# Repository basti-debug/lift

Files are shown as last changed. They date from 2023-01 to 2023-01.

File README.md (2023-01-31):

# Liftsteuerung

*** 

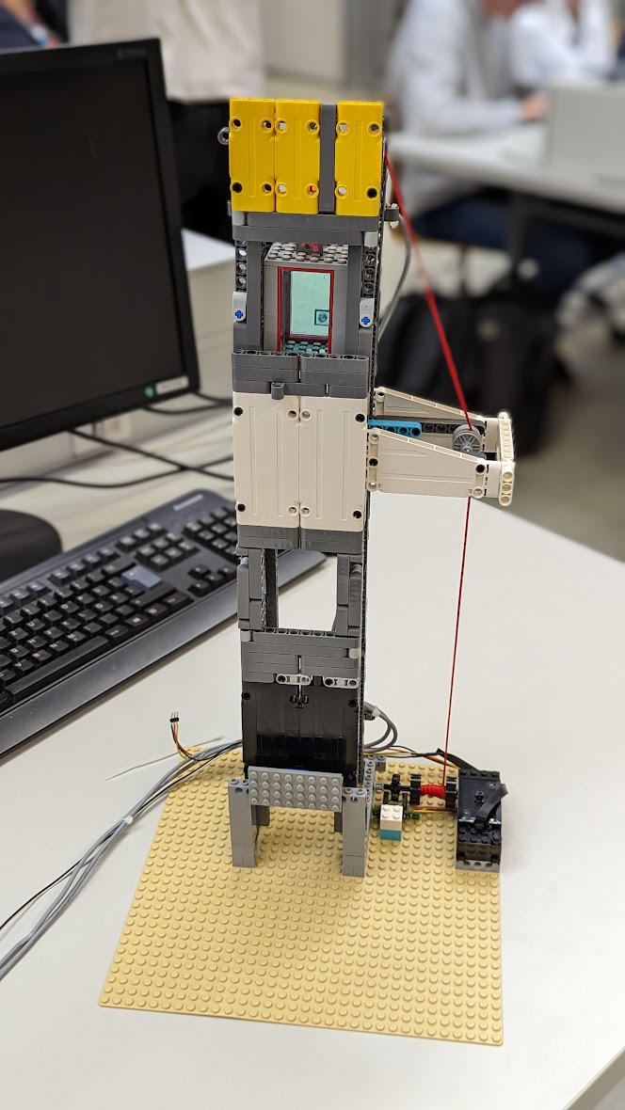
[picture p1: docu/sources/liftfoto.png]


Projektmitglieder: 
* Sebastian Mayrhofer / *zuständig für Hardware und Dokumentation*
* Joel Rupp / *zuständig für Software*

 **HTL Rankweil**  4chel                                                                 Schuljahr 2022-23 

***

[TOC]

***

## Aufgabenstellung 
*verfasst von Sebastian Mayrhofer*

Im Projekt "Liftsteuerung" wird dass Konzept einer Liftsteuerung in Miniatur umgesetzt. Der Lift soll mit Hilfe von Lego Componenten und einer MegaCard gesteuert werden. Mit Hilfe einer Lichtschranke soll die Position der Kabine herausgefunden werden. Ebenfalls wird ein Hall Sensor als Endstop genutzt. 

## Umsetzung 
Uns wurde ein motorisierter Liftschacht aus Lego zur Verfügung gestellt. Wir haben den Liftschacht verstärkt und der Kabine Rollen montiert, die die Fahrt stabilisieren sollen. 

### Benutztes Material

* Lego-Steine  (Lift Schacht und Kabine) 
* MEGACard  (Steuerung des Motors, auswertung der Sensoren)
* Hall Sensor (End-Stop)
* Lichtschranke (Stockwerkbestimmung)

### Stockwerk-bestimmung (Lichtschranke)

Da nach einem Reset die Position des Liftes unbekannt ist, muss irgendwie ein bestimmer Zustand hergestellt werden. Dies ist bei uns so realisiert, indem der Aufzug nach unten fährt, bis der untere Endstop auslöst. Dann wir die Höhe genullt

Um die Stockwerke genau zu bestimmen, benutzen wir, wie vorgegeben, eine Lichtschranke. Diese Lichtschranke wurde unterbrochen durch ein Lego Technik Teil das wir direkt auf Antriebsachse (Winden Achse) gesteckt haben.

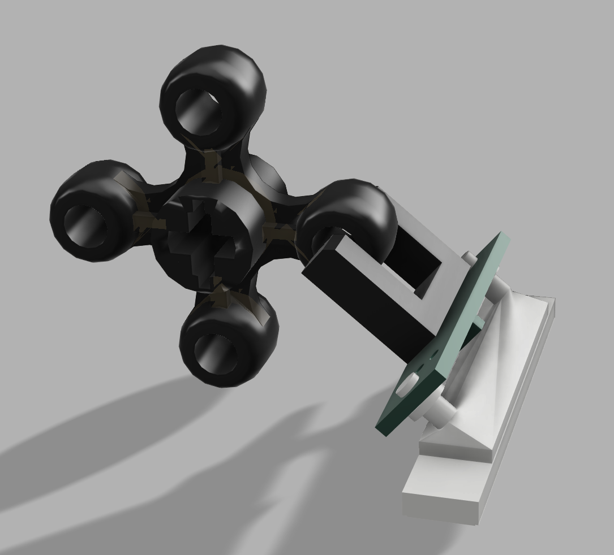
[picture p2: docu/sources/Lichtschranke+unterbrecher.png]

*Lichtschranke Halterung mit Unterbrecher*

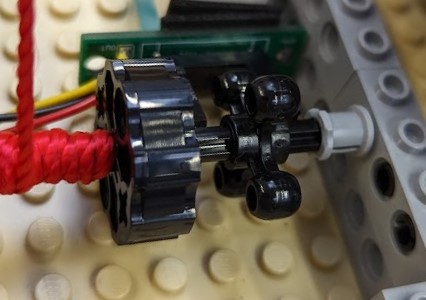
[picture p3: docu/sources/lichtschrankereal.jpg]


*realer Aufbau*

**Wie Messen wir mit Hilfe der Lichtschranke ?** 

Mit Hilfe eines externen Interrupts der auf die fallende Flanke des Sensors (also das Unterbrechen der Lichtschranke) konfiguriert ist können wir die zurückgelegten Umdrehungen, und somit das aktuelle Stockwerk bestimmen.

### Endstops -Sebastian

Mit Hilfe eines HallSensoren im untersten Stock wurde ein Endstop realisiert. Dieser wird Benutzt um die Position der Kabine, nach einem Reset bzw Neustart der MegaCard, zu bestimmen. 

Der uns zur Verfügung gestellte Hall Sensor: 

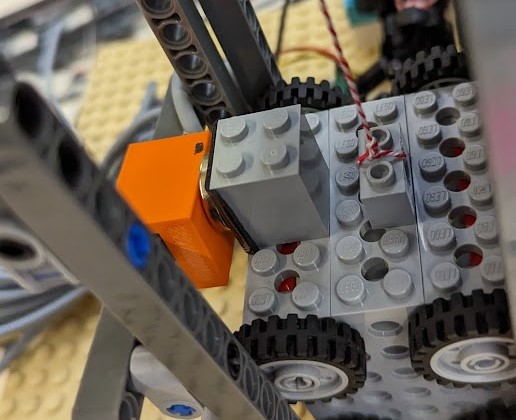
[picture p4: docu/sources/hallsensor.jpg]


*in orange, der Hall Sensor*

Dieser wird ausgelöst durch einen Magnet der an der Kabine befestigt ist. Hierdurch können wir die Software kalibrieren und den Null Punkt festlegen. 

### Motor Ansteuerung
*ab hier von Joel Rupp verfasst*

Wir steuern den Aufzug Motor, einen Lego Eisenbahn Motor, mit Hilfe eines Motortreibers an, dieser ist an PC6 und PC5 zur Steuerung angeschlossen, als auch zweimal an VCC und einmal an GND

### Verkabelung 

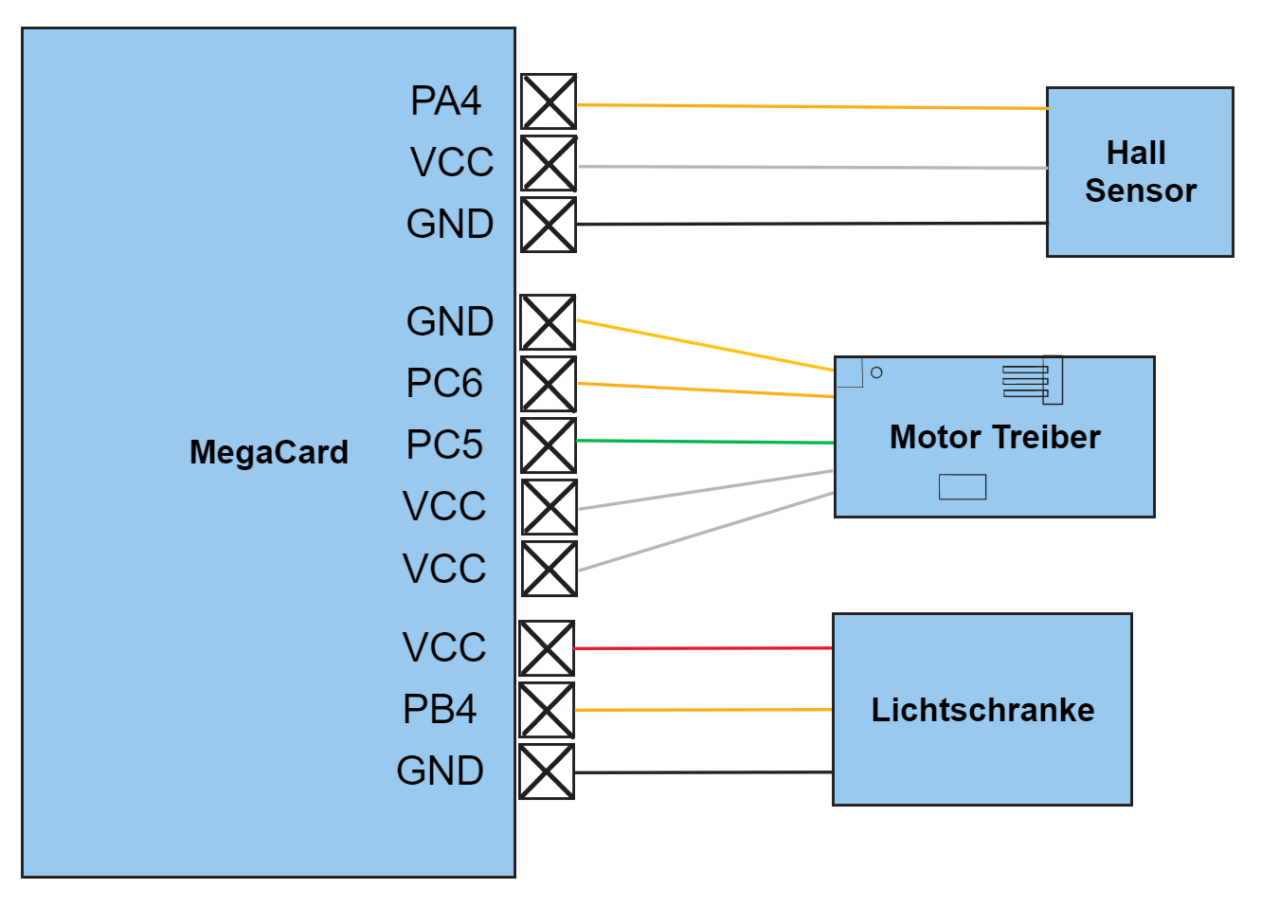
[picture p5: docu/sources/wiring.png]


### Probleme 

Wenn oft zwischen den Stockwerken 1 und 2 hin- und hergefahren wird, kann ein Fehler beobachtet werden, welcher immer großer wird. Wenn ins Erdgeschoss gefahren wird, wird dieser Fehler zurückgesetzt. Eine mögliche Erklärung dieses Fehlers folgt nun. 

~~~c
if (direction==2)	//Falls nach oben gefahren wird
	{
		heightticks++;	//Zählvariable erhöhen
	}
	if (direction==1)	//Falls nach unten gefahren wird
	{
		heightticks--;	//Zahlvariable verkleinern
	}
~~~
*Code in der ISR der Lichtschranke*

Da beim Auslesen der Lichtschranke keine Richtung bekannt ist, wird diese bei uns anhand der eingestellten Drehrichtung des Motors bestimmt. Wenn nun der Motor gestoppt wird, bleibt dieser aber nicht sofort stehen. Dadurch kann es passieren, dass der Geber in die nächste Stufe "rutscht", dies aber nicht erfasst wird. Wenn dies nur in eine Richtung passiert, addiert sich der Fehler

### System-Hierarchie 

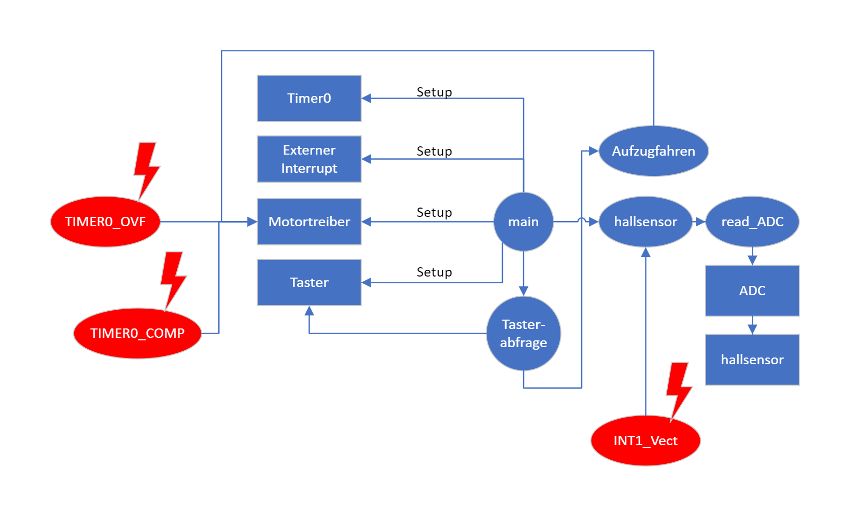
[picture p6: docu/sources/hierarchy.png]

*Die Interrupts sind Rot eingefärbt*

### Mögliche Verbesserungen 
* Es könnte noch ein Hallsensor als oberer Endstop verwendet werden, dies würde den Fehler beheben
* Um den Kabelsalat zu beseitigen könnte eine Adapterplatine designed werden, welche nur auf die MegaCard aufgesteckt werden müsste
* Mit der MegaCardV5 oder neuer könnte das Display benutzt werden, um Fahrtrichtung und Stockwerk anzuzeigen
* Ein Softwarereset könnte über einen Watchdogtimer realisiert werden, um im Fehlerfall automatisch zu resetten

# Anleitung Lift

## Anschlussdiagram:

*zu beachten ist die Orientierung des Motor Treibers, zu sehen and dem makierten rechteck und den Kreis im linken oberen Eck*
## Funktionsbeschreibung
* Reset: Nach einem Reset fährt der Aufzug in das Erdgeschoss hinunter.
* Taster 0-2: Die Tasternummer gibt das Stockwerk an, in welches gefahren werden soll.
* LEDs: Anhand der LEDs kann die aktuelle Ansteuerung des Motors gesehen werden. Wenn beide leuchten wird gebremst, ansonsten wird gefahren. 

## Mehr Informationen

* Repository: https://github.com/basti-debug/lift

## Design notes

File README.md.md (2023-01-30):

# Liftsteuerung

*** 



Projektmitglieder: 
* Sebastian Mayrhofer / *zuständig für Hardware und Dokumentation*
* Joel Rupp / *zuständig für Software*

 **HTL Rankweil**  4chel                                                                 Schuljahr 2022-23 

***

[TOC]

***

## Aufgabenstellung 

Im Projekt "Liftsteuerung" wird dass Konzept einer Liftsteuerung in Miniatur umgesetzt. Der Lift soll mit Hilfe von Lego Componenten und einer MegaCard gesteuert werden. Mit Hilfe einer Lichtschranke soll die Position der Kabine herausgefunden werden. Ebenfalls wird ein Hall Sensor als Endstop genutzt. 

## Umsetzung -Joel

Uns wurde ein motorisierter Liftschacht aus Lego zur Verfügung gestellt. Wir haben den Liftschacht verstärkt und der Kabine Rollen montiert, die die Fahrt stabilisieren sollen. 

### Benutztes Material

* Lego-Steine  (Lift Schacht und Kabine) 
* MEGACard  (Steuerung des Motors, auswertung der Sensoren)
* Hall Sensor (End-Stop)
* Lichtschranke (Stockwerkbestimmung)

### Stockwerk-bestimmung (Lichtschranke)

Um die Stockwerke genau zu bestimmen, benutzen wir, wie vorgegeben, eine Lichtschranke. Diese Lichtschranke wurde unterbrochen durch ein Lego Technik Teil das wir direkt auf Antriebsachse (Winden Achse) gesteckt haben.


*Lichtschranke Halterung mit Unterbrecher*



*realer Aufbau*

**Wie Messen wir mit Hilfe der Lichtschranke ?** 

Mit Hilfe eines externen Interrupts der auf die fallende Flanke des Sensors (also das Unterbrechen der Lichtschranke) konfiguriert ist können wir die zurückgelegten Umdrehungen, und somit das aktuelle Stockwerk bestimmen.

### Endstops 

Mit Hilfe eines HallSensoren im untersten Stock wurde ein Endstop realisiert. Dieser wird Benutzt um die Position der Kabine, nach einem Reset bzw Neustart der MegaCard, zu bestimmen. 

Der uns zur Verfügung gestellte Hall Sensor: 


*in orange, der Hall Sensor*

Dieser wird ausgelöst durch einen Magnet der an der Kabine befestigt ist. Hierdurch können wir die Software kalibrieren und den Null Punkt festlegen. 

### Motor Ansteuerung -Joel
Wir steuern den Aufzug Motor, einen Lego Eisenbahn Motor, mit Hilfe eines Motortreibers an, dieser ist an PC6 und PC5 zur Steuerung angeschlossen, als auch zweimal an VCC und einmal an GND

### Verkabelung 



### Probleme -Joel

Wenn oft zwischen den Stockwerken 1 und 2 hin- und hergefahren wird, kann ein Fehler beobachtet werden, welcher immer großer wird. Wenn ins Erdgeschoss gefahren wird, wird dieser Fehler zurückgesetzt. Eine mögliche Erklärung dieses Fehlers folgt nun. 
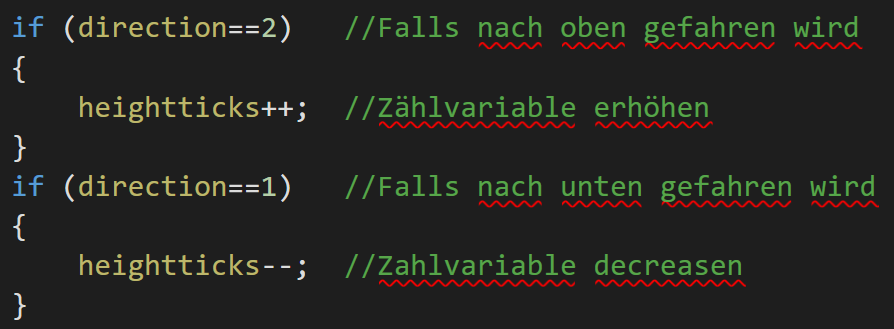
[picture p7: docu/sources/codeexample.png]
 Code in der ISR der Lichtschranke

Da beim Auslesen der Lichtschranke keine Richtung bekannt ist, wird diese bei uns anhand der eingestellten Drehrichtung des Motors bestimmt. Wenn nun der Motor gestoppt wird, bleibt dieser aber nicht sofort stehen. Dadurch kann es passieren, dass der Geber in die nächste Stufe "rutscht", dies aber nicht erfasst wird. Wenn dies nur in eine Richtung passiert, addiert sich der Fehler

### System-Hierarchie -Joel


Die Interrupts sind Rot eingefärbt

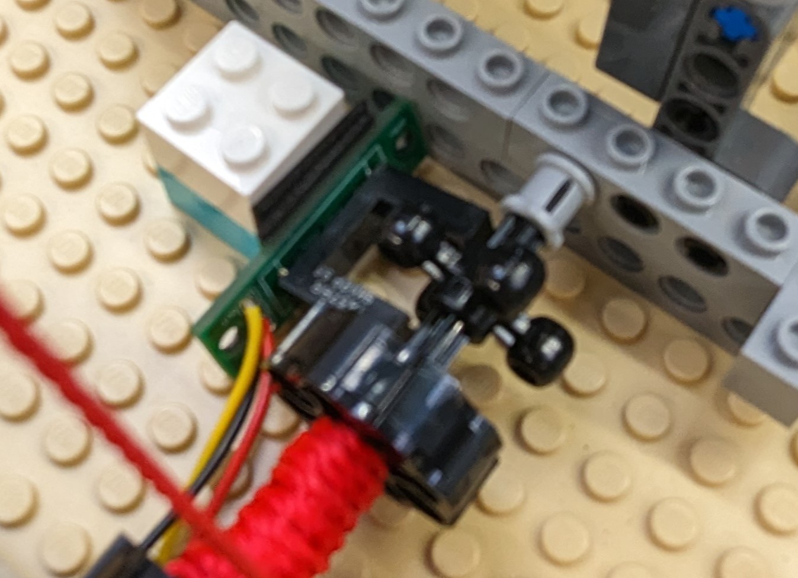
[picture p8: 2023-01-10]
docu/sources/endstopfoto.jpg

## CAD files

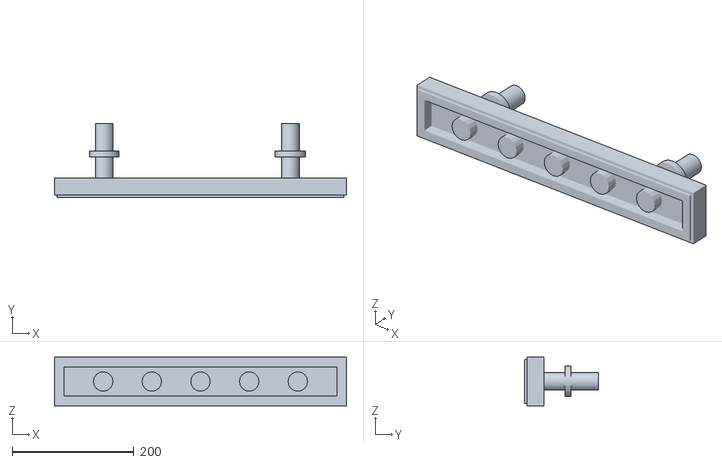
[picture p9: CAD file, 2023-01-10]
parts/lichtschrankeholder v2.stl
480.0 x 121.0 x 80.0

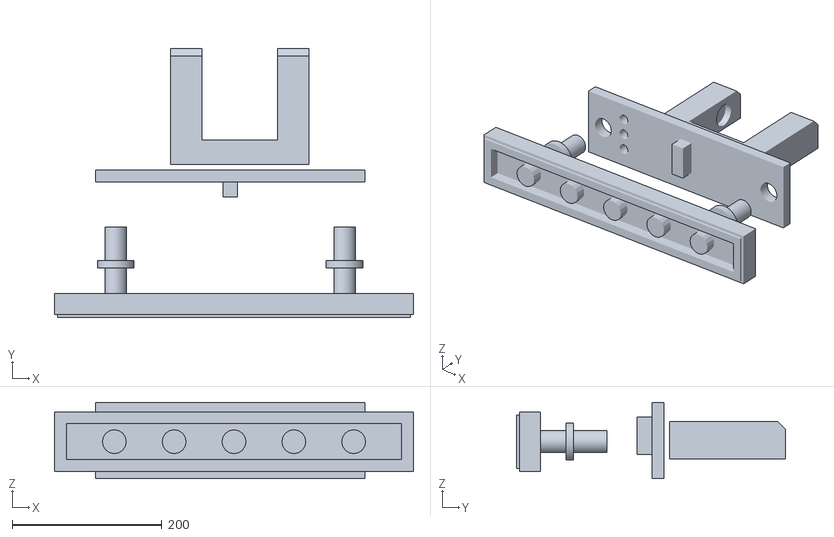
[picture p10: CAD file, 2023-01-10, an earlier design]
parts/lichtschrankeholder v1.stl
480.0 x 359.0 x 102.2

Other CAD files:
parts/lichtschrankeholder v5.f3d

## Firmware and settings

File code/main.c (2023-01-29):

/*
 * Motorsteuerung-test.c
 *
 * Created: 06/12/2022 10:37:38
 * Author : joelr
 * eventuell noch Reset über Taste realisieren (mit Watchdog-Timer???)
 * KeyPad: Weiß an PB0
 */ 

#include <avr/io.h>
#include <util/delay.h>
#include <avr/interrupt.h>

#define DOWN (0x40)
#define UP (0x20)
#define BRAKE (0x60)
#define FREE (0x00)

#define Stock0 0	//Höhe des 0. Stockes in Drehimpulsticks
#define Stock1 31	//Höhe des 1. Stockes in Drehimpulsticks
#define Stock2 60	//Höhe des 2. Stockes in Drehimpulsticks

#define HallKanalUnten 4	//Eingangskanal für den unteren Hallsensor

volatile unsigned char direction=0;	//Bit für die Richtung, 2=Aufwärts/1=Abwärts/0=Stillstand
volatile unsigned int heightticks=1000;	//Zählvariable für die Höhe, bzw. die Umdrehungen des Motors
volatile unsigned char stockwerk=0;	//Variable für das aktuelle Stockwerk

unsigned char read_ADC8(unsigned char kanal)
{
	unsigned char wert = 0;
	DDRA &= ~(1<<kanal);    //übergebener Kanal auf Eingang
	ADCSRA &= ~(1<<ADATE); //Einzelwandlung
	ADCSRA |= (1<<ADPS0) | (1<<ADPS1) | (1<<ADPS2);        //Hardwareteiler auf 128 setzen = 93,75kHz
	ADCSRA |= (1<<ADEN);    //ADC-Wandler einschalten
	ADMUX |= (1<<ADLAR);    //Wandlungsergebniss linksbündig
	ADMUX &= (~(1<<MUX3) & (~(1<<MUX4)));    //MUX-Kanal einstellen: unipolar
	ADMUX &= ~(1<<MUX0) & ~(1<<MUX1) & ~(1<<MUX2); //ADMUX kanäle rücksetzen
	ADMUX |= kanal;        // ADMUX mit kanal verodern, somit die kanäle setzen
	ADMUX |= (1<<REFS0);     // Referenz auf 5V
	ADCSRA |= (1<<ADSC);    //Wandlung starten
	while (ADCSRA & (1<<ADSC)){;};        //Warten, solange Wandlung im Gange ist
	wert = ADCH;                     //Wert ausgeben
	ADCSRA &= ~(1<<ADEN);    //Wandler ausschalten
	return wert;            //ADC-Wert übergeben
}

unsigned char hallsensor(){		//Gibt "1" zurück wenn der Lift am unteren Hallsensor steht und "0" falls weder noch
	//Unterer Hall Sensor
	if (read_ADC8(HallKanalUnten)<=30)	{return 1;}		//Wenn der untere Hallsensor ausgelöst hat
	
	else if ((read_ADC8(HallKanalUnten)>=100))	{return 0;}	//Wenn beide nicht ausgelöst haben
	return 0;	//Fehlerhafte Messung
}

ISR(INT1_vect)		//Wird bei fallender Flanke an PD3 ausgeführt
{
	switch(heightticks){		//Stockwerk nach den Heightticks setzen
		case Stock1: stockwerk=1; break;
		case Stock2: stockwerk=2; break;
		default: break;
	}
	if (hallsensor()==1)
	{
		stockwerk=0;
		heightticks=0;
	}
	
	if (direction==2)	//Falls nach oben gefahren wird
	{
		heightticks++;	//Zählvariable erhöhen
	}
	if (direction==1)	//Falls nach unten gefahren wird
	{
		heightticks--;	//Zahlvariable decreasen
	}
}

ISR(TIMER0_OVF_vect){		//Wird beim Overflow des Timers aufgerufen
	if (direction==2){		//Wenn aufwärts gefahren wird
		PORTC&=~(DOWN);	//Bitweise invertieren um zwischen Brems und Aufwärtsfahren zu wechseln
	}
	if (direction==1){		//Wenn abwärts gefahren wird
		PORTC&=~(UP);	//Bitweise invertieren um zwischen Brems und Aufwärtsfahren zu wechseln
	}
	if (direction==0){		//Wenn der Lift steht
		PORTC|=BRAKE;			//Bremsen
	}
}

ISR(TIMER0_COMP_vect){		//Wird aufgerufen wenn der Timer OCR0 erreicht
	if (direction==2){		//Wenn aufwärts gefahren wird
		PORTC|=(DOWN);	//Bitweise invertieren um zwischen Brems und Aufwärtsfahren zu wechseln
	}
	if (direction==1){		//Wenn abwärts gefahren wird
		PORTC|=(UP);	//Bitweise invertieren um zwischen Brems und Aufwärtsfahren zu wechseln
	}
	if (direction==0){		//Wenn der Lift steht
		PORTC|=BRAKE;			//Bremsen
	}
}



void AufzugFahren(unsigned char zielstockwerk){
	
	switch(heightticks){		//Stockwerk nach den Heightticks setzen
		case Stock0: stockwerk=0; break;
		case Stock1: stockwerk=1; break;
		case Stock2: stockwerk=2; break;
		default: break;
	}
	
	while (stockwerk>zielstockwerk)	//Wenn das aktuelle Stockwerk über dem Zielstockwerk liegt e.g. Aktuell: 1 Ziel:0
	{
		direction=1; // Richtung: abwärts
		OCR0=80;     // Geschwindigkeit abwärts
	}
	while (stockwerk<zielstockwerk)	//Wenn das aktuelle Stockwerk unter dem Zielstockwerk liegt
	{
		direction=2; // Richtung: aufwärts
		OCR0=220;    // Geschwindigkeit aufwärts 
	}
	
	direction=0;
}
//Gibt beim gedrücktem Taster die Nummer zurück. Falls keiner gedrückt ist "3"
unsigned char tasterabfrage(){ 
	
	if (!(PINA&0x01)) {			//Taster S0		Erdgeschoss anfahren
		return 0;
	}
	else if (!(PINA&0x02)) {	//Taster S1		1. Stock anfahren
		return 1;
	}
	else if (!(PINA&0x04)){		//Taster S2		2. Stock anfahren
		return 2;
	}
	else if (!(PINA&0x08)){		//Taster S3
	}
	return 3;
}
int main(void)
{
	//IOs konfigurieren
	#pragma region
		DDRC=0xff;		//C-Register auf Ausgang setzen (LEDs, Motortreiber)
		PORTC=0x00;		//Alle Ausgänge im C-Register LOW setzen
		DDRA=0x00;		//A-Register auf Eingang setzen (Taster)
		PORTA=0x07;		//Pullups für S0...S4 einschalten
		DDRD=0x00;				//DDR-D auf Eingang
		PORTD=(1<<PD3);			//Pullup für INT1-Pin
	#pragma endregion
	
	//Interrupt 0 konfigurieren
	#pragma region Interrupt-Config
	GICR|=(1<<INT1);		//INT1 freigeben
	MCUCR|=(1<<ISC11);		//INT1 falling edge
	MCUCR&=~(1<<ISC10);		//INT1 falling edge
	#pragma endregion Interrupt-Config
	
	//Timer0 konfigurieren
	#pragma region Timer0-Config
	TCCR0|=(1<<CS02)|(1<<CS00);		//Timer0 Systemtakt/1024
	TIMSK|=(1<<TOIE0)|(1<<OCIE0);		//Overflow und Match Interrupt freigeben
	TCCR0|=(1<<WGM01)|(1<<WGM00);		//FastPWM
	OCR0=230;
	#pragma endregion Timer0-Config
	
	sei();					//Interrupt global freigeben
	
	//Am Start ins Erdgeschoss fahren, da der Anfangszustand sonst unbekannt ist
	while (hallsensor()!=1)
	{
		direction=2;
	}
	direction=0;
	heightticks=0;		//Heightticks nullen, da der Aufzug jetzt sicher im Erdgeschoss steht
	
    while (1) //Arbeitsschleife
    {
		switch(tasterabfrage()){		//Stockwerk nach den Heightticks setzen
			case 0: AufzugFahren(0); break;
			case 1: AufzugFahren(1); break;
			case 2: AufzugFahren(2); break;
			case 3: break;
			default: break;
		}
    }
}

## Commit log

2023-01-10 added docu and parts
    [lichtschrankeholder v1.stl, lichtschrankeholder v2.stl]
2023-01-29 added wiring docu
2023-01-29 lichtsensor halterung v5
    [lichtschrankeholder v5.f3d]
2023-01-29 added docu hall and light sensor
2023-01-31 changed wiring picture
